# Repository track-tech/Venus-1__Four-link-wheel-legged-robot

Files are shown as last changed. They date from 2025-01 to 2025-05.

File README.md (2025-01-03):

# 启明-1 四连杆轮腿机器人 | Venus-1  Four-link wheel-legged robot

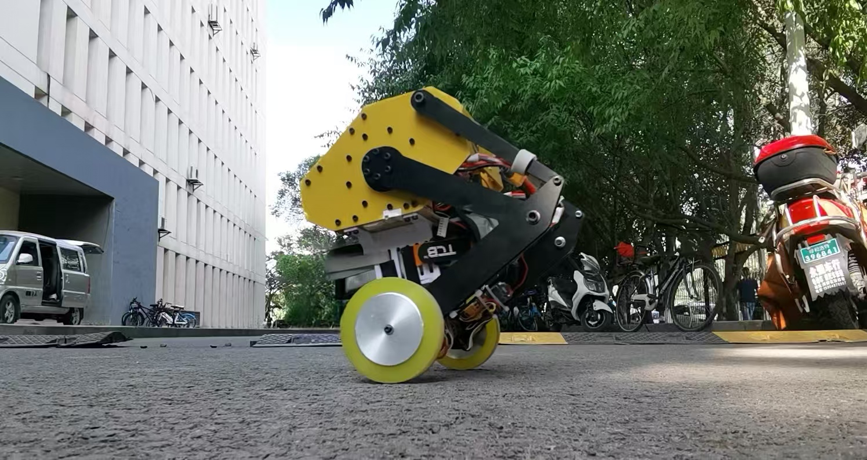
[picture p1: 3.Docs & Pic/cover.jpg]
Real Robot


## 0x00 声明&介绍

该项目为**个人本科毕业设计**，由于时间与个人能力不足，**存在设计缺陷**，请谨慎复刻。

项目遵循**GPL 3.0**协议，量产及商业使用需授权

> 演示视频合集
>[Venus轮腿机器人视频合集]: https://space.bilibili.com/21198864/lists/4193332?type=series
> 

**概况**

- 机械建模使用Soildworks2024 sp0.1绘制，使用请注意软件版本
- 基于STM32H723 HAL库开发，使用FreeRTOS进行任务管理
- 关节电机使用小米CyberGear微电机，轮电机使用DJI C610+M2006 P36
- 外壳及主要结构均使用3mm 3240环氧板（玻纤板），高强度
- 完全使用PID控制
- 机器人遥控使用FS-I6X 主控通过SBUS与接收机FS-IA6B通信
- 基本采用商业模块构件，拼装快速

------

### 机体测试

#### 重心自适应

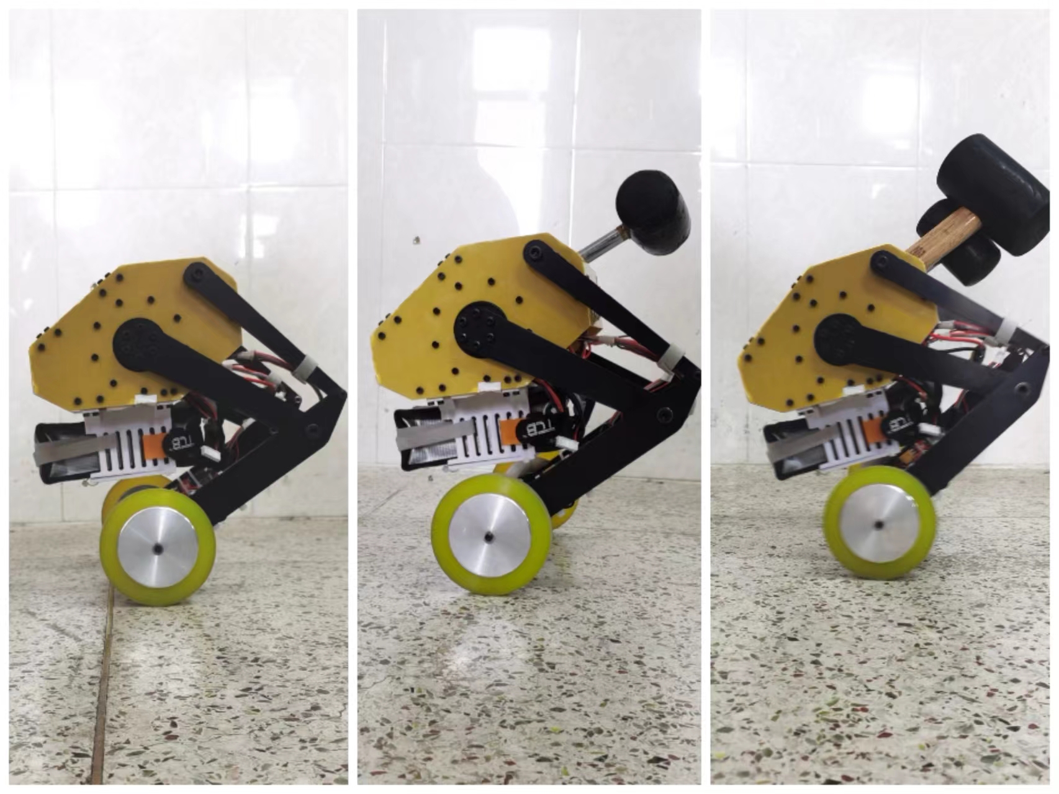
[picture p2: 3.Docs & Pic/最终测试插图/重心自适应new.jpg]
重心自适应new


#### 下落缓冲测试

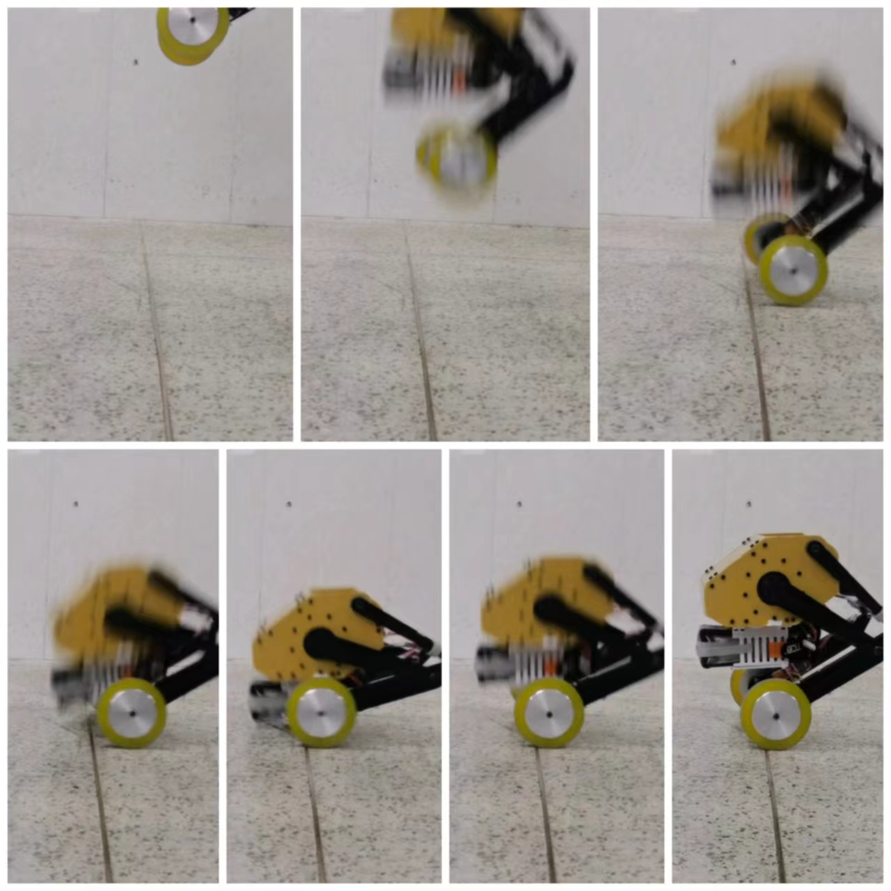
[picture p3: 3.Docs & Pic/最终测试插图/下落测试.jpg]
下落测试


#### 主动悬挂测试（Roll角自稳定）

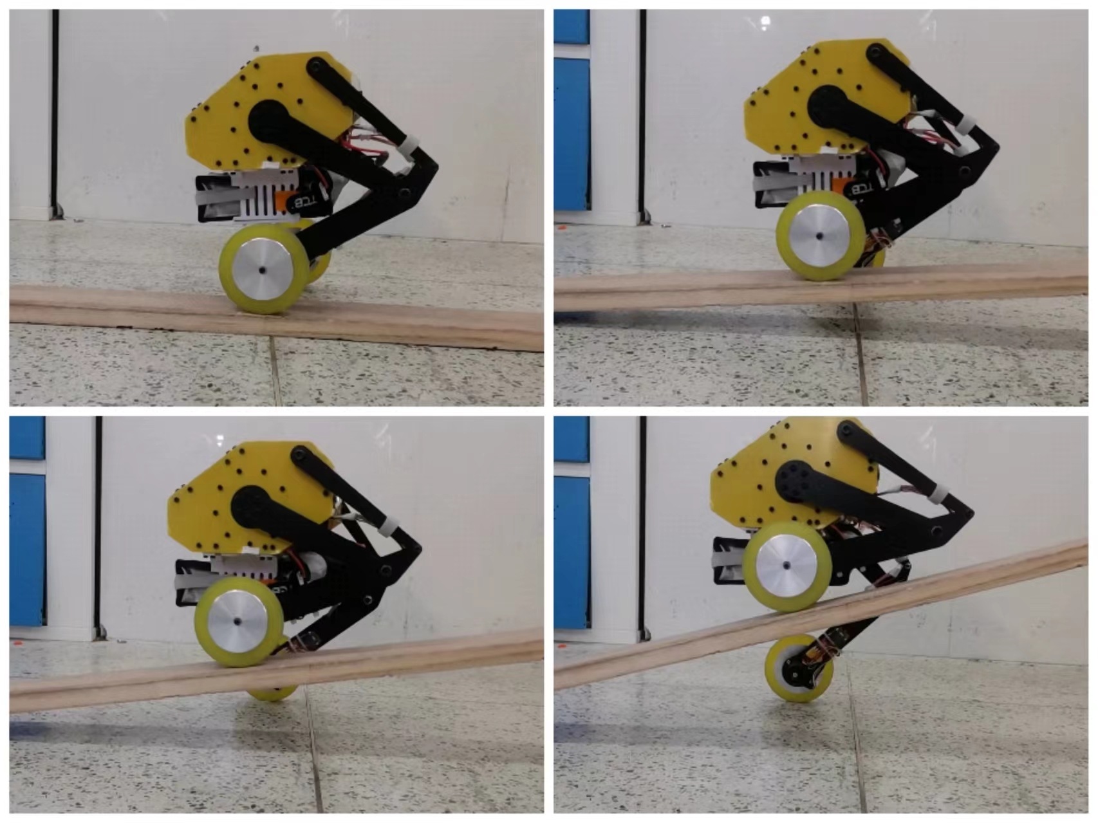
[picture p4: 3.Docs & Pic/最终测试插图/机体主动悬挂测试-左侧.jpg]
机体主动悬挂测试-左侧


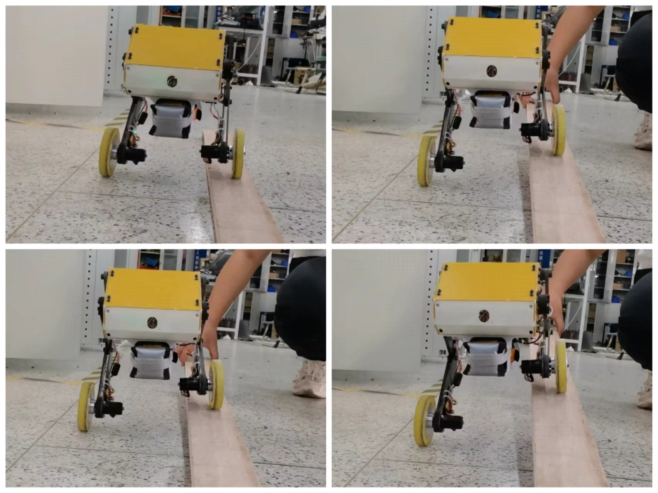
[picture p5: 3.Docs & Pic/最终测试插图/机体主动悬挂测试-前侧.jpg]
机体主动悬挂测试-前侧


#### 跳跃测试

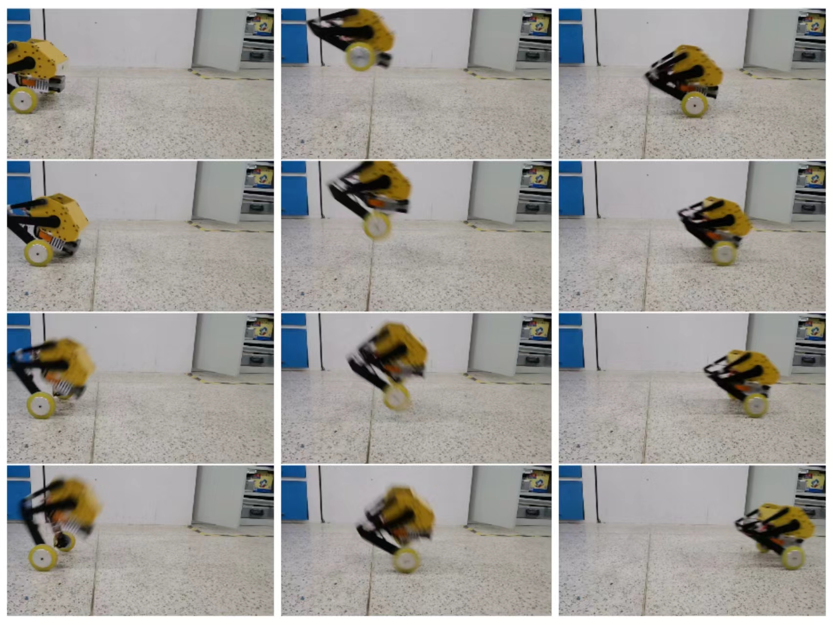
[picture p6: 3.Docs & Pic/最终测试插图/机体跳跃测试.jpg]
机体跳跃测试


## 0x01 机械结构

主体结构使用3mm 3240环氧树脂板及六面四方螺母固定，电气仓3D打印制成

### 连杆设计

连杆由Pyslvs拟合后，在Soildworks中建模

> [Pyslvs官网]: https://pyslvs-ui.readthedocs.io/en/stable/

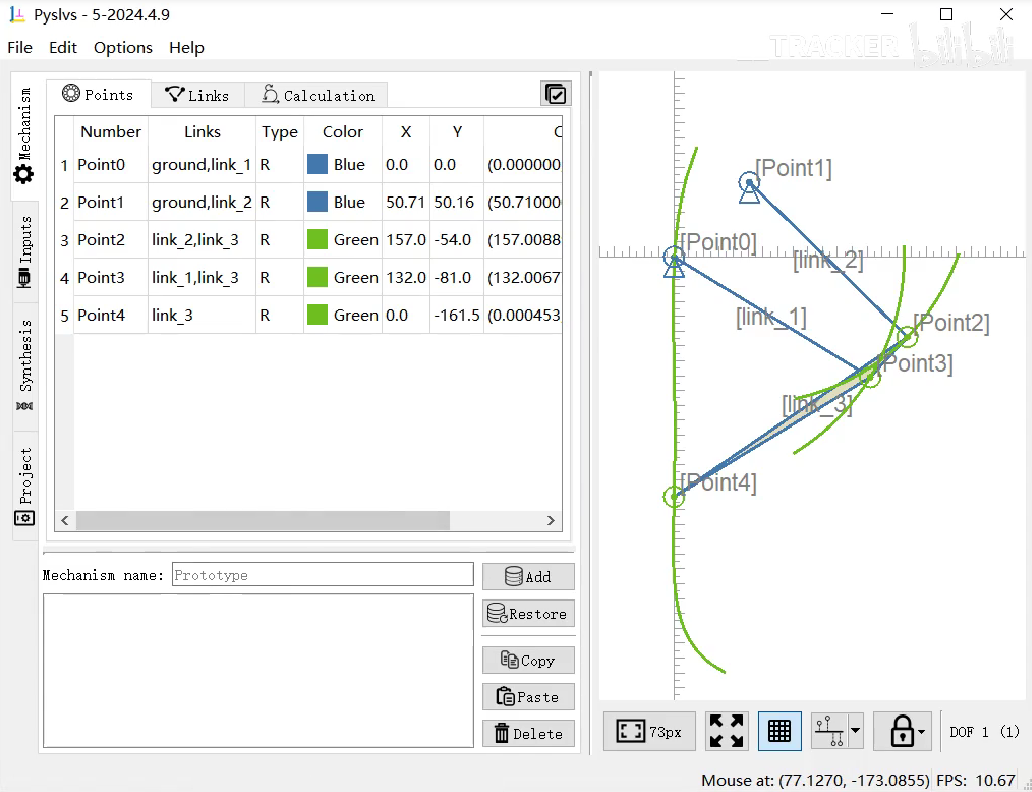
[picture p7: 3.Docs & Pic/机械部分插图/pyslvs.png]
pyslvs
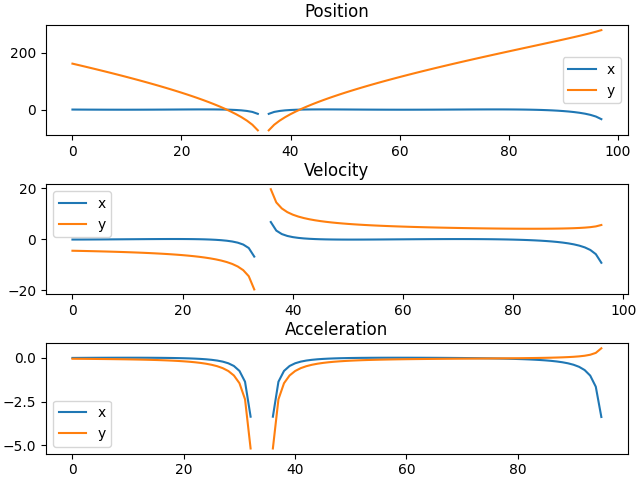
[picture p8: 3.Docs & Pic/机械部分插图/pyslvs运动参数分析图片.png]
pyslvs运动参数分析图片
|  |  |
| --- | --- |

### 三维简图

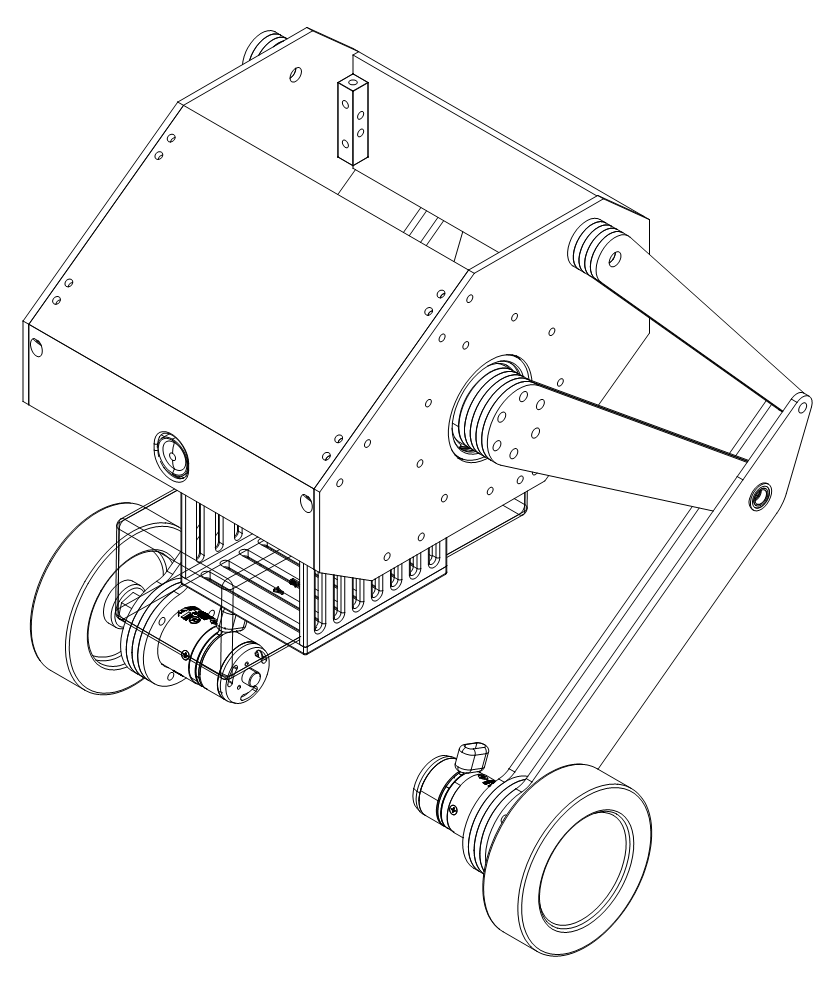
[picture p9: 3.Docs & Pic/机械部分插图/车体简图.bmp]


| 电器仓示意 | 截面视图 |
| :---: | :---: |
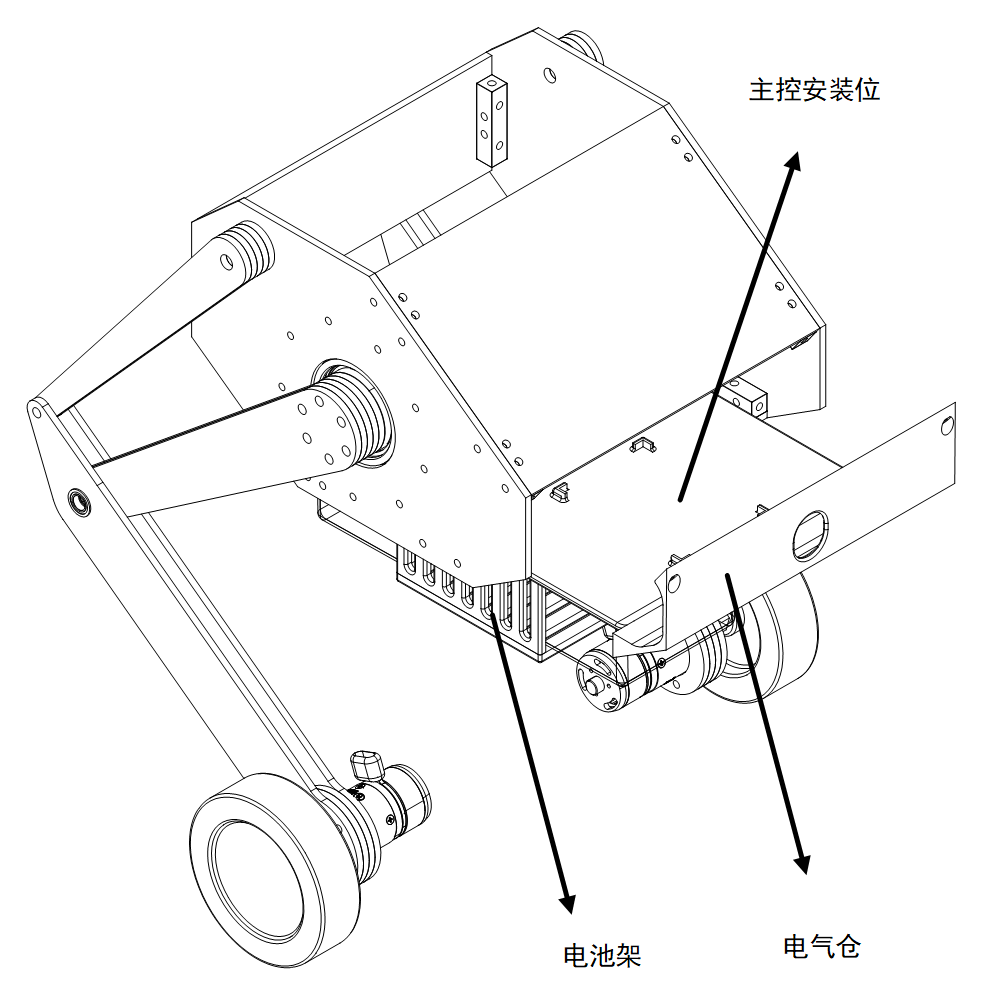
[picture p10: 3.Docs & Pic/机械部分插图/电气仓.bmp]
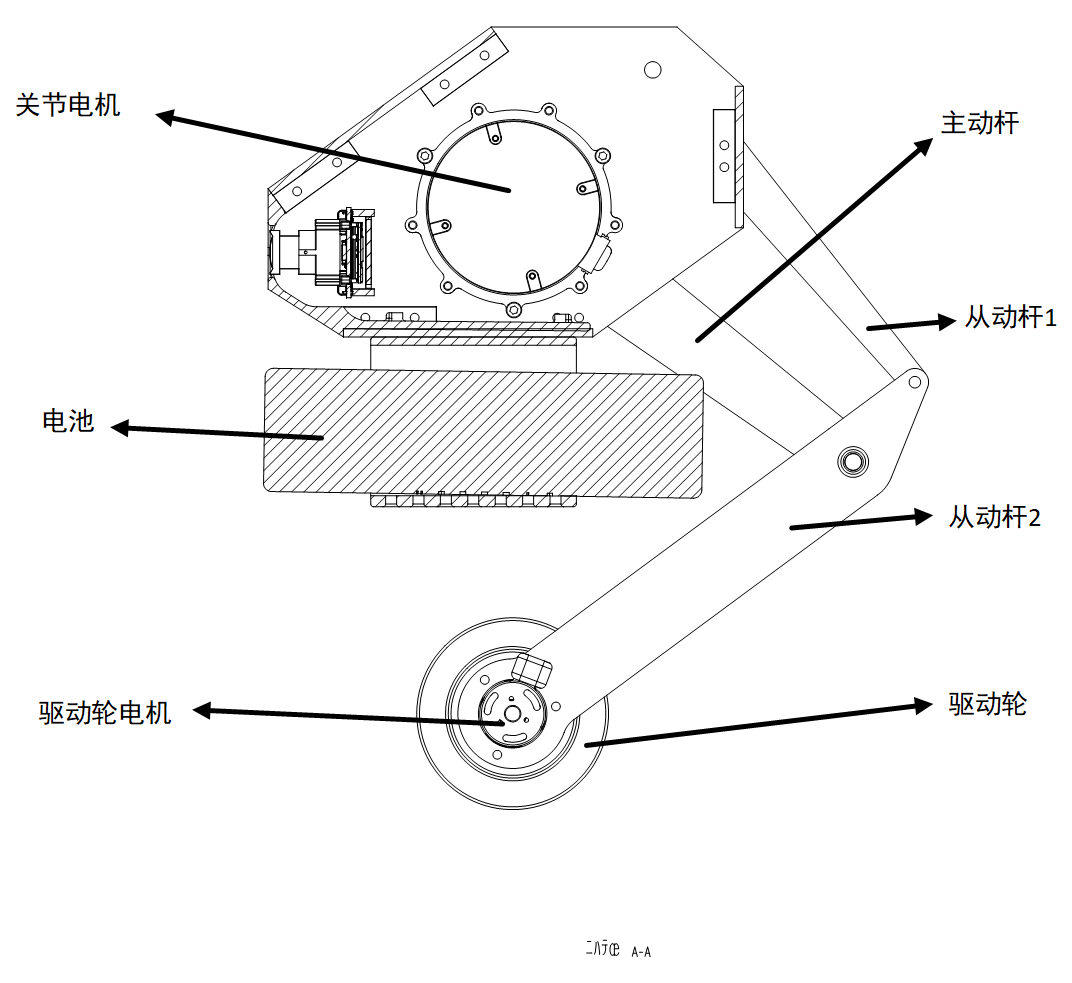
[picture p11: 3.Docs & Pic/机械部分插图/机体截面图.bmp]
|  |  |

## 0x02 电气连接

系统电源以及CAN总线通过中心分电板集合分配，下图为连接示意：

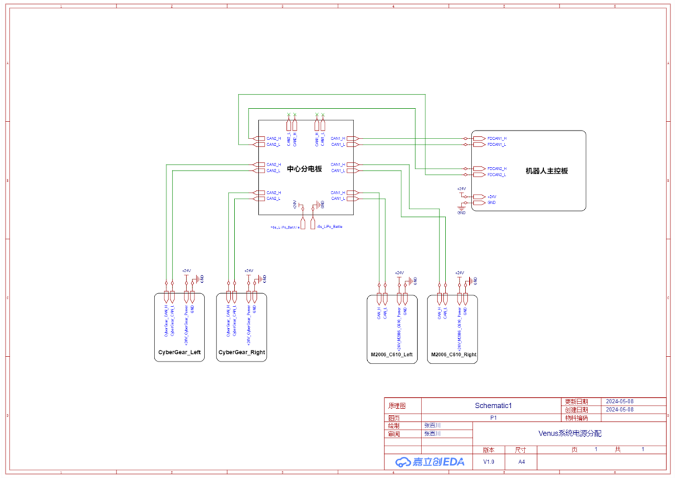
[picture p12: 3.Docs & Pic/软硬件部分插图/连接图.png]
连接图


使用到的中心分电板同样是之前顺便画的

>分电板开源链接
>[XT60/XT30分电板 | CAN Bus分线板]: https://oshwhub.com/marktracker/xt60-xt30-fen-dian-ban-can-fen-xian-ban
>
>

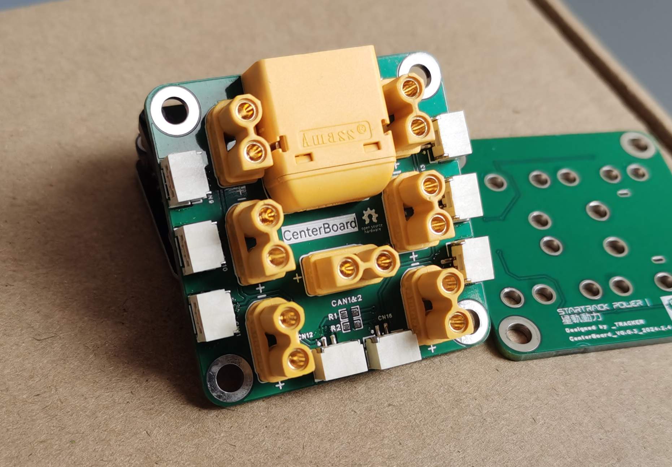
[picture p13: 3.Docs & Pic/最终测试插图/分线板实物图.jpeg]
分线板实物图


| 实物装配图-1 | 实物装配图-2 |
| :---: | :---: |
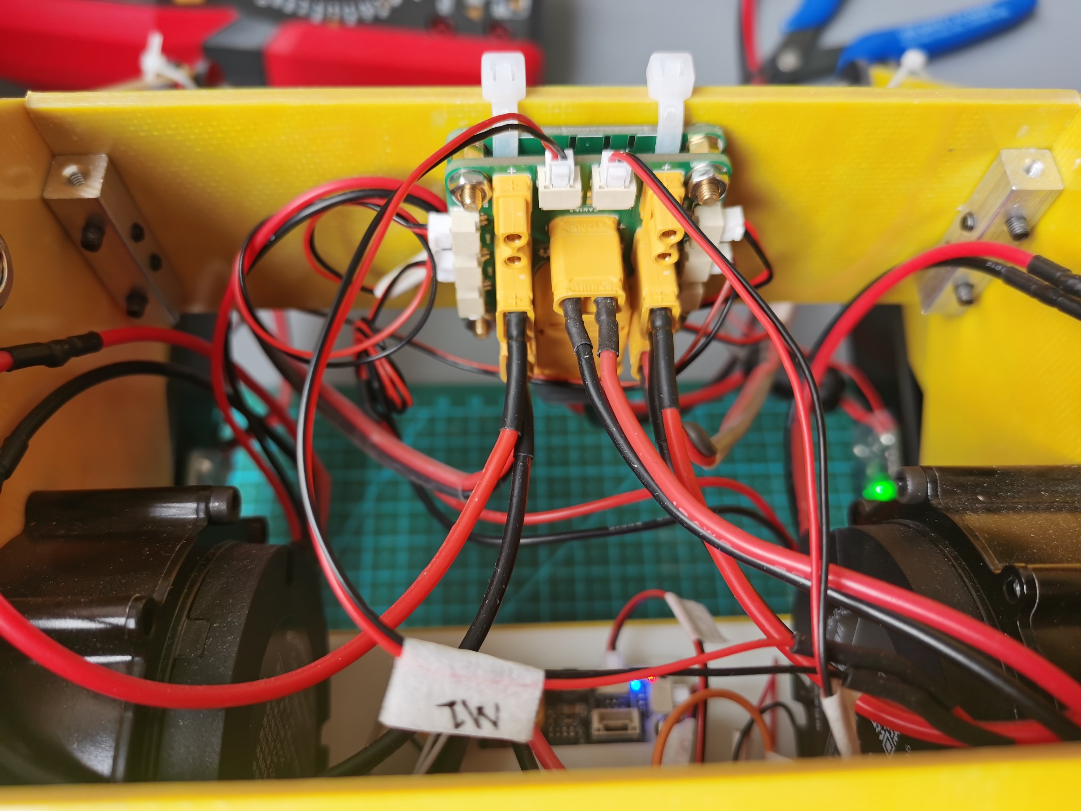
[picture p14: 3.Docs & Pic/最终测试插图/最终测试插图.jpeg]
最终测试插图
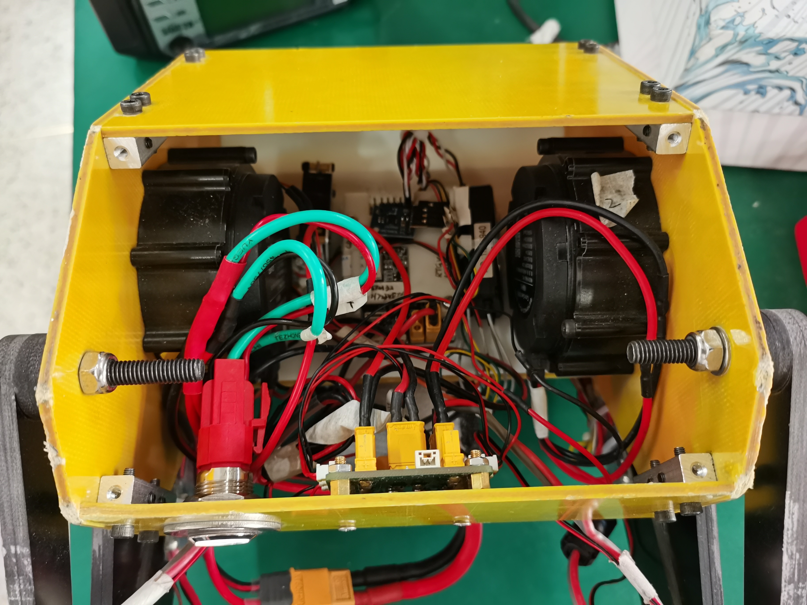
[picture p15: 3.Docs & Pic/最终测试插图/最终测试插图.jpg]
最终测试插图
|  |  |

## 0x03 软件架构

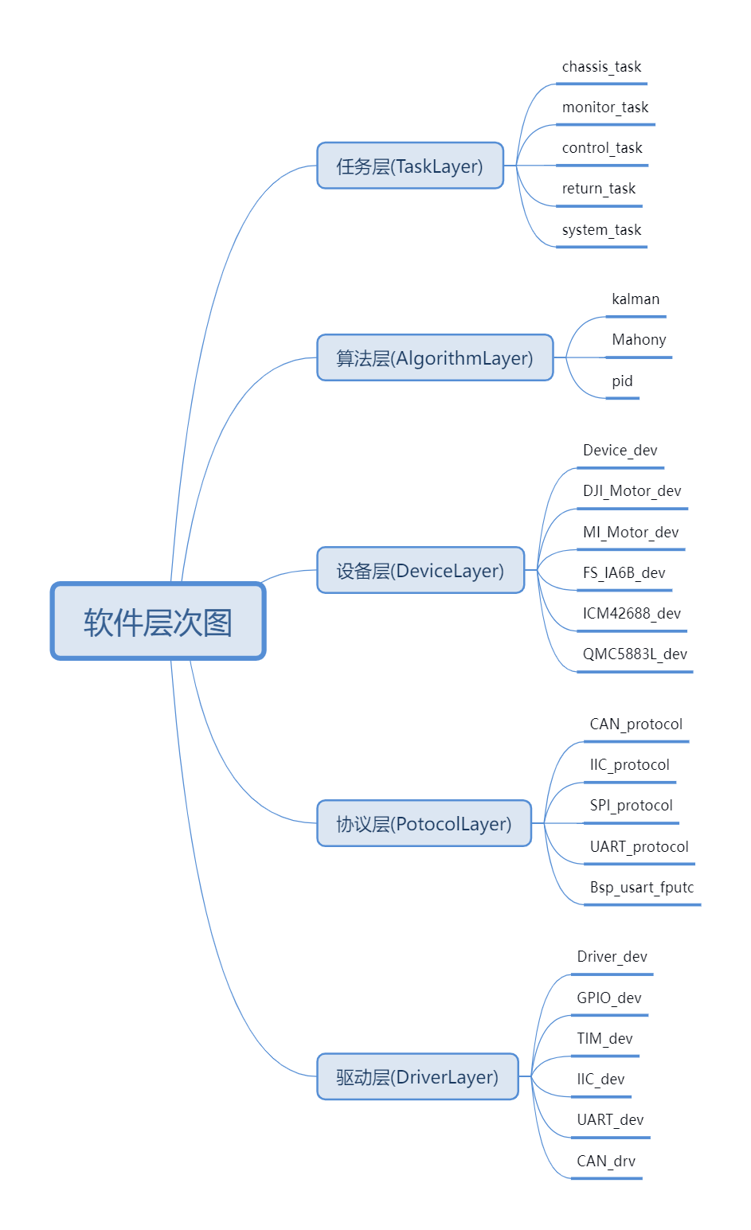
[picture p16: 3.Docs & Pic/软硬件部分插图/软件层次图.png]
软件层次图


软件整体分为五大块，具体见完整程序工程

## 0x04 参考成本&已知缺陷报告

### 参考成本表格

| 物料名 | 单价（RMB） | 数量 | 总价（RMB） |
| --- | --- | ---- | --- |
| CyberGear微电机 | 499 | 2 | 998 |
| DJI M2006动力套装（C610+M2006 P36） | 159+275=434 | 2 | 868 |
| 主控开发板 宇昌电子YCMC-H7A（STM32H723+ICM42688）/或改用达妙DM-MC02（STM32H723+BMI088 IMU型号不同，需重构） | 259(YCMC-H7A) | 1 | 259 |
| 3240环氧板定制费用（由于经过多次修改，具体费用不明，这里给出大致参考价格） | 200 | 1 | 200 |
| 轴承+螺栓螺母大致费用 | 40 | 1 | 40 |
| 中心分电板（自制嘉立创免费打板） | 10 | 1 | 10 |
| 连接用线束+接口 | 25 | 1 | 25 |
| 24V35C航模锂电 TCB | 176 | 1 | 176 |
| 遥控富斯FS-I6X+接收机FS-IA6B(遥控可替换为PS2无线遥控，或者其他类) | 251+56=301 | 1 | 301 |
| | | 合计 | 2877（除去遥控为2576） |

上述均为全新价格，可以去二手平台买旧的，可以更便宜

### 已知缺陷

**由于机器人现已放于学校，故无法进一步改进，下面是测试过程中发现的一些问题用于参考**

- 选用的驱动轮电机M2006减速箱齿隙较大，导致整体机身会在平衡点高速抖动，难以改善，我选用这个完全是由于经济条件限制，用了之前的旧电机，推荐直接使用大扭矩的云台电机作为驱动轮电机
- CyberGear为单编码电机，每次重新上电需要重新标定机械零点，该机器人通过轮电机与主体底板的限制，通过监测关节电机扭矩变化来确定是否到达零点，没有添加额外的限位块
- 演示视频与建模使用的轮并不一致，实物使用聚氨酯包胶轮规格 直径90mm 轮胶面宽16mm 内径6mm ，实测连接不稳定，最好使用3D打印轮毂，自制包胶轮
- Yaw轴漂移未解决，使用的CyberGear电机概率出现初始化指令不接收，原因未知，电机群群友似乎也有这种情况
- 电器仓正面开的洞是为M2Dock准备的，用于目标识别和路径跟踪（最后没时间加了）

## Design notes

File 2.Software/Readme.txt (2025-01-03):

工程文件使用STM32CubeMX生成基础框架&移植FreeRTOS，使用KEIL5编辑工程文件
任务函数运行周期见cubemx配置

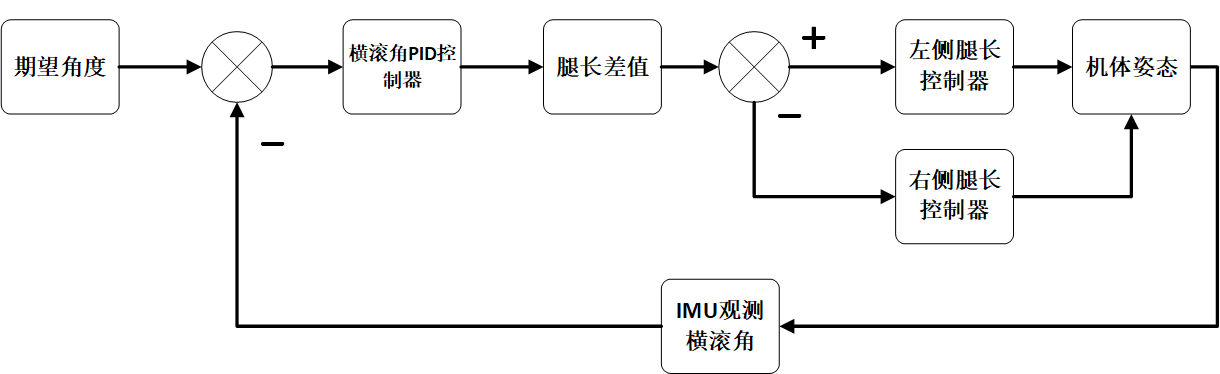
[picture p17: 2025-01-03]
3.Docs & Pic/控制部分插图/横滚角控制器.bmp

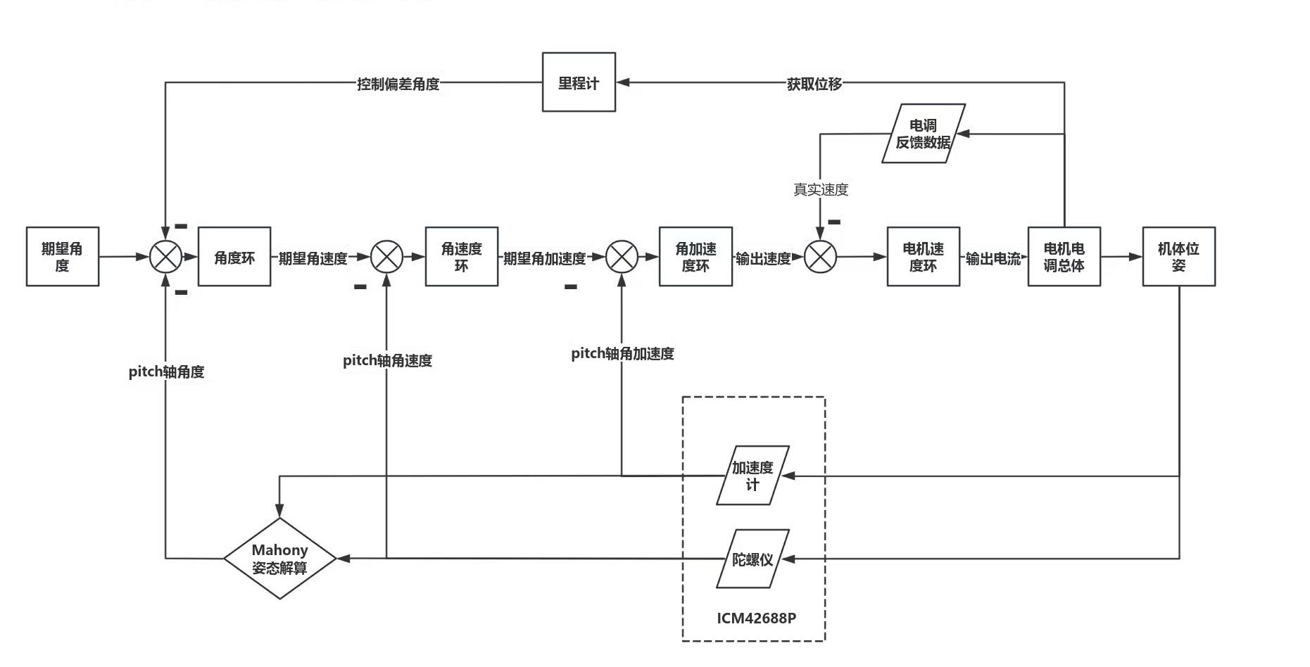
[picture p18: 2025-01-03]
3.Docs & Pic/控制部分插图/PID平衡控制器.jpg

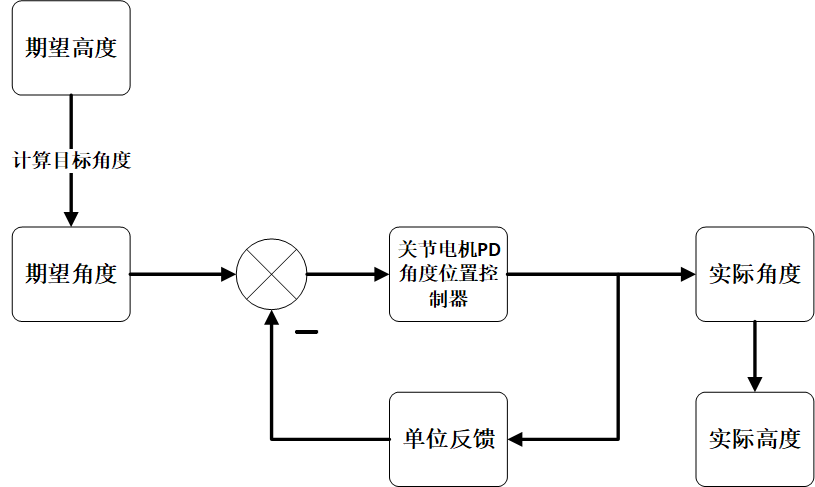
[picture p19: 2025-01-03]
3.Docs & Pic/控制部分插图/单腿高度控制.bmp

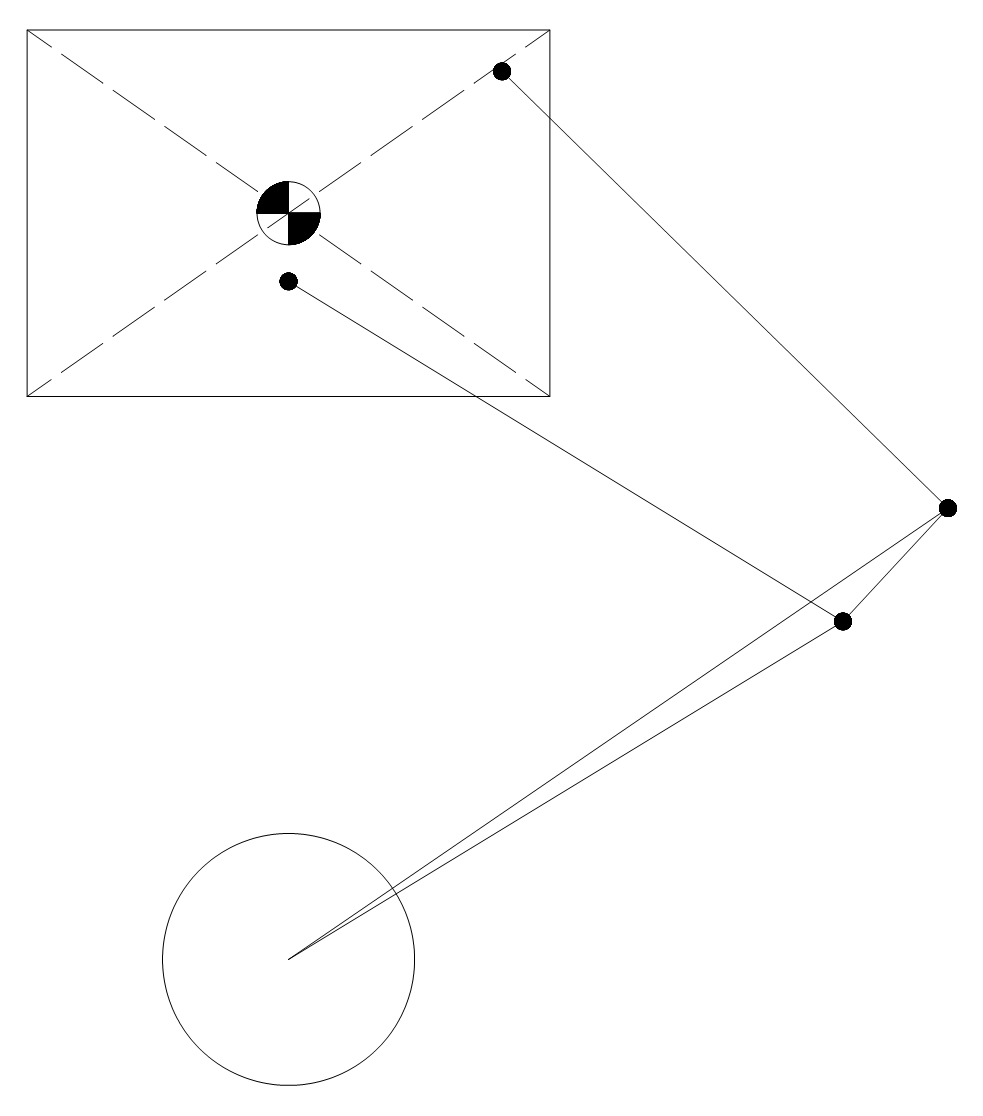
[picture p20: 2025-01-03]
3.Docs & Pic/机械部分插图/机器人简图.bmp

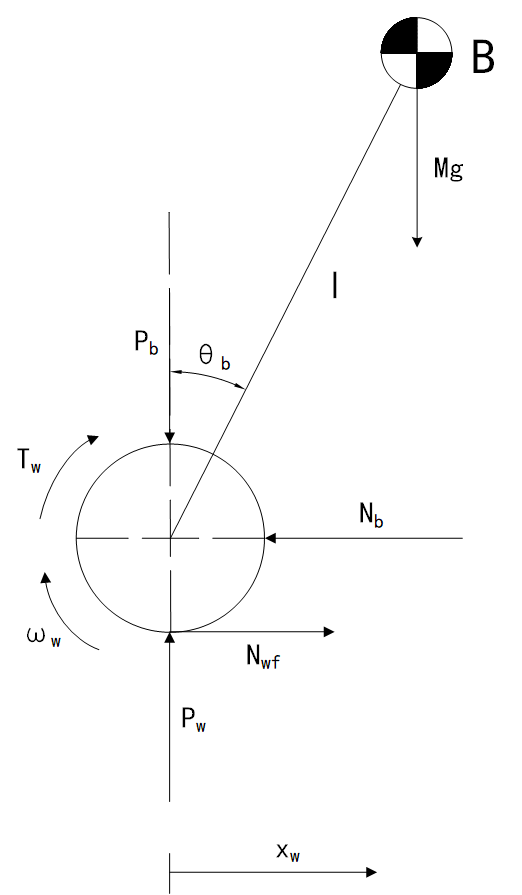
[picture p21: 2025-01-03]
3.Docs & Pic/机械部分插图/建模简图.bmp

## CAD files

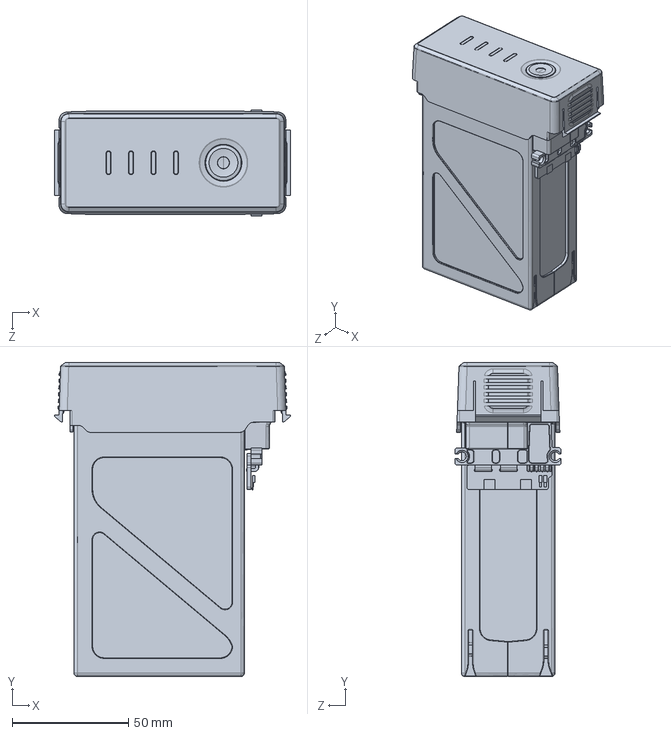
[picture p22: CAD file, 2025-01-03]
1.3D_Model/大疆电池-弃用/电池装配.SLDASM
101.5 x 134.8 x 45.5 mm

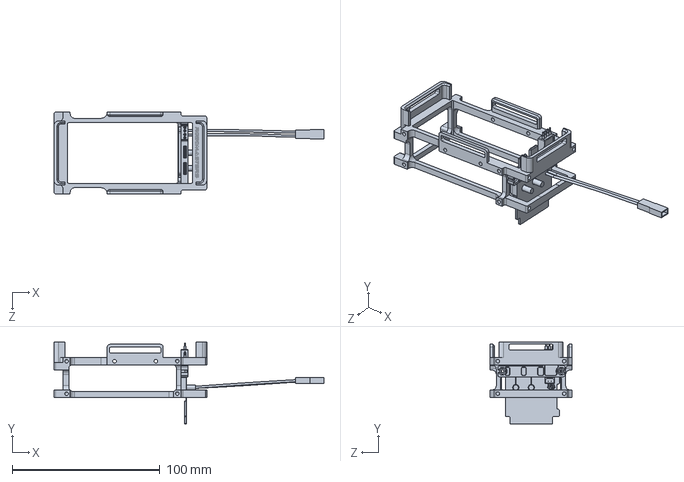
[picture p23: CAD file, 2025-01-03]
1.3D_Model/大疆电池-弃用/Rm新版电池架（带开关）.SLDPRT
182.9 x 55.5 x 55.4 mm

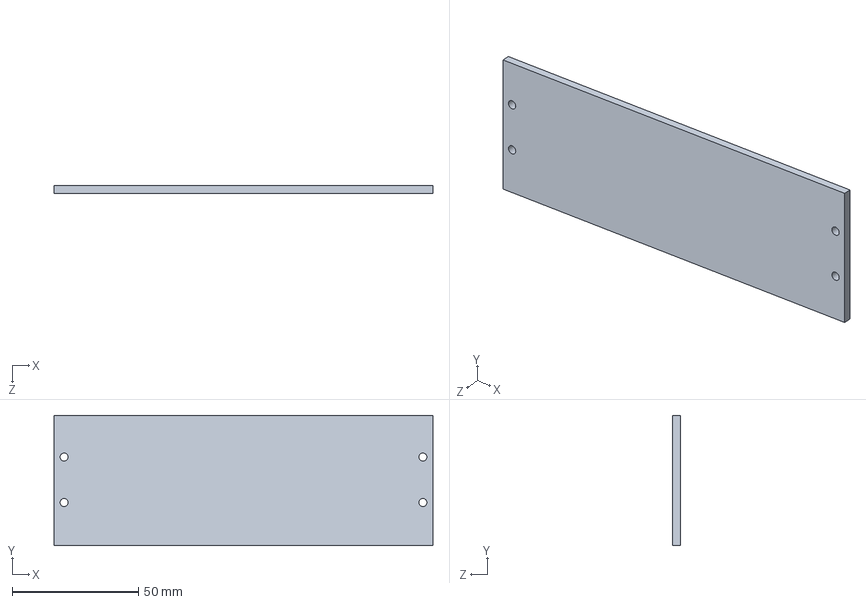
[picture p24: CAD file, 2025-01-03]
1.3D_Model/机架/后盖板^Venus_总装设计_原比例0.6倍_2023.10.17.SLDPRT
150.0 x 51.6 x 3.00 mm

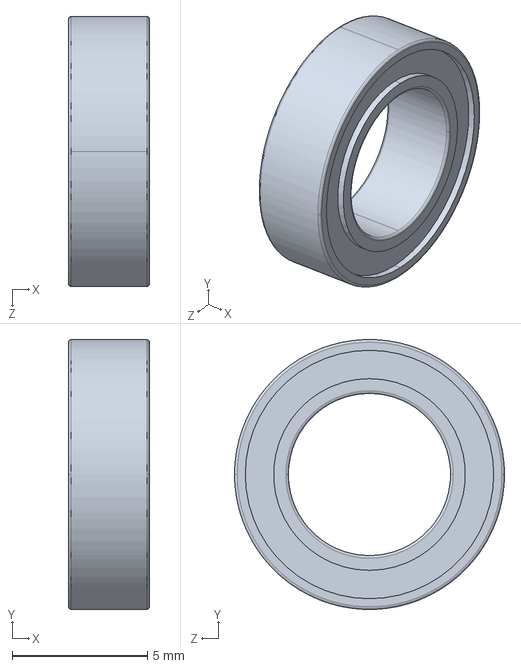
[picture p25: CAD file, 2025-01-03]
1.3D_Model/深沟球轴承 bca bcas[bca-a6-d10-b3].SLDPRT
3.00 x 10.0 x 10.0 mm

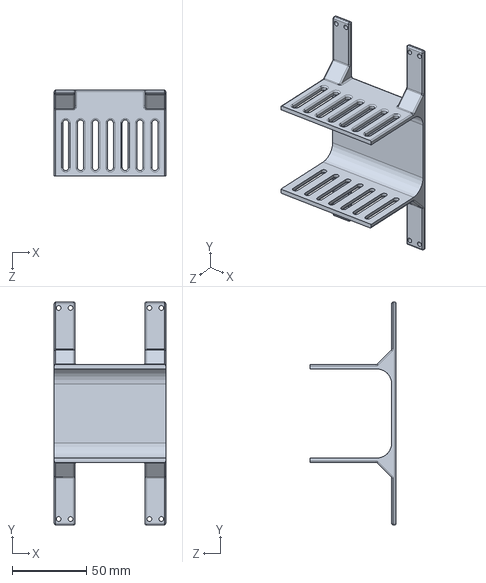
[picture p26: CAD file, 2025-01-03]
1.3D_Model/电池支架拆分/电池支架底座.SLDPRT
75.0 x 150.0 x 58.0 mm

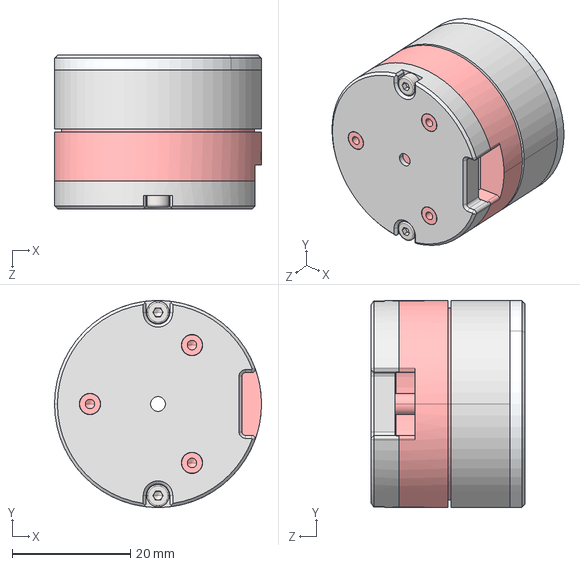
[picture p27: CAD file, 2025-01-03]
1.3D_Model/脉塔电机模型-原方案/2806/RMD-2806.STEP
35.0 x 35.0 x 26.0 mm

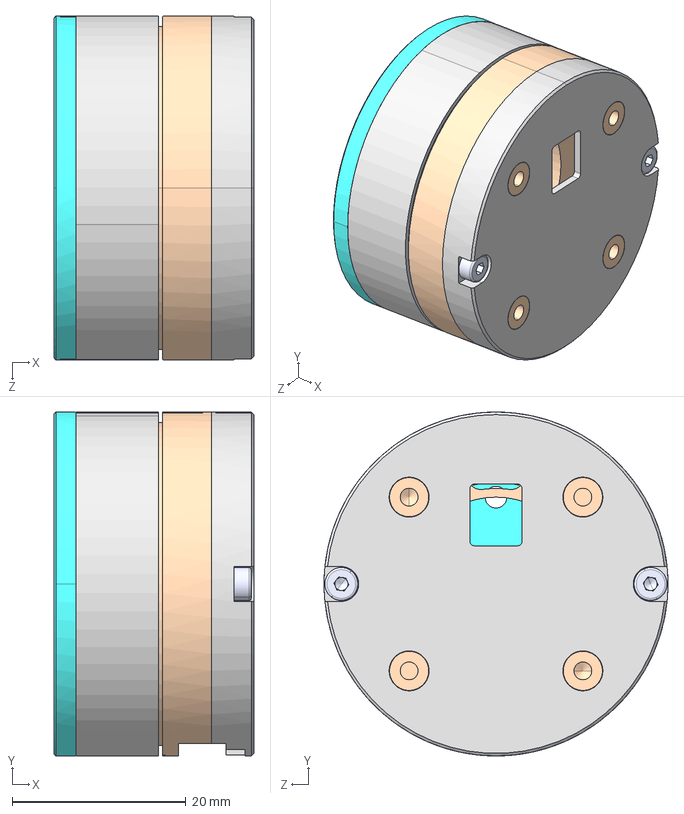
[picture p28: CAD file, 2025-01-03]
1.3D_Model/脉塔电机模型-原方案/4005/RMD-4005 .STEP
23.0 x 39.6 x 39.6 mm

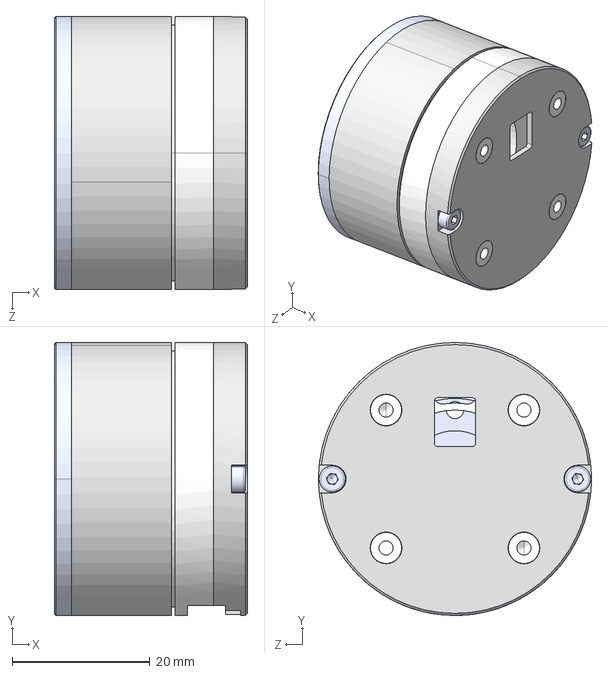
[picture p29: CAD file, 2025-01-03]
1.3D_Model/脉塔电机模型-原方案/4010/RMD-4010.STEP
28.0 x 39.6 x 39.6 mm

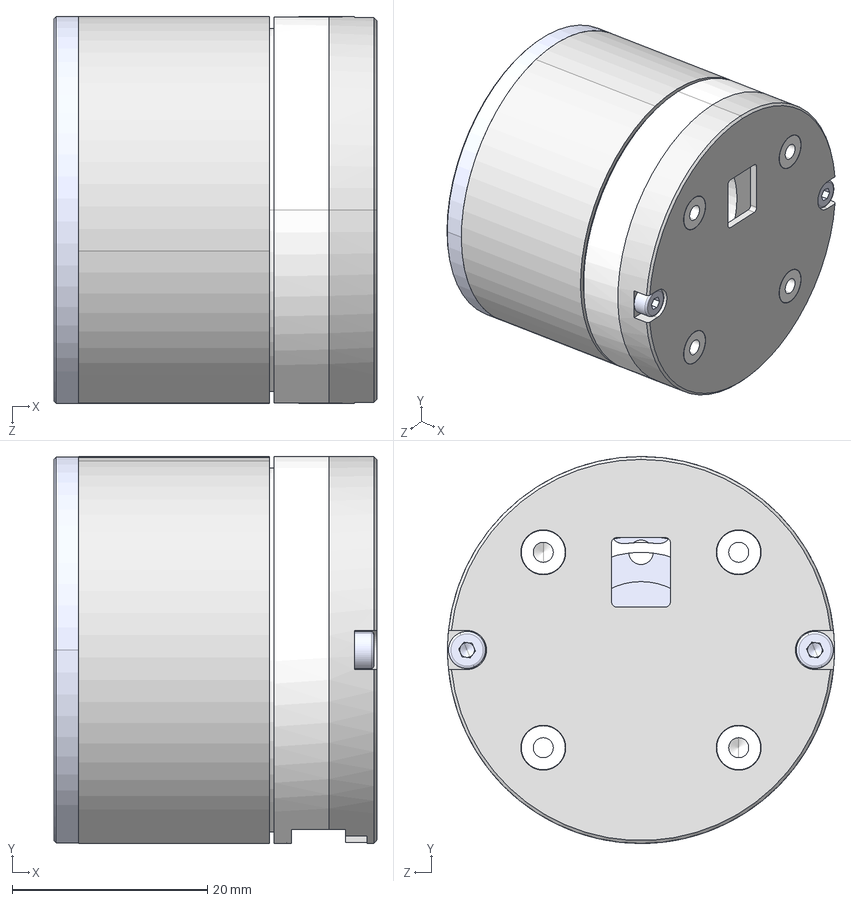
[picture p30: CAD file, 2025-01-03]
1.3D_Model/脉塔电机模型-原方案/4015/RMD-4015.STEP
33.0 x 39.6 x 39.6 mm

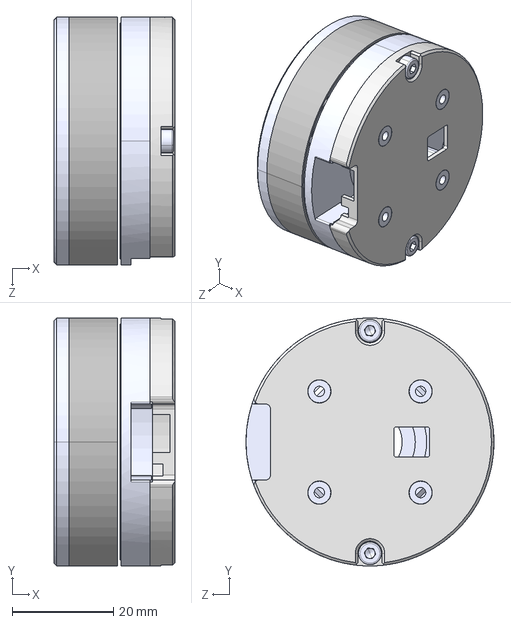
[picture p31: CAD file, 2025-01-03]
1.3D_Model/脉塔电机模型-原方案/5005/RMD-S-5005.STEP
23.9 x 49.0 x 49.0 mm

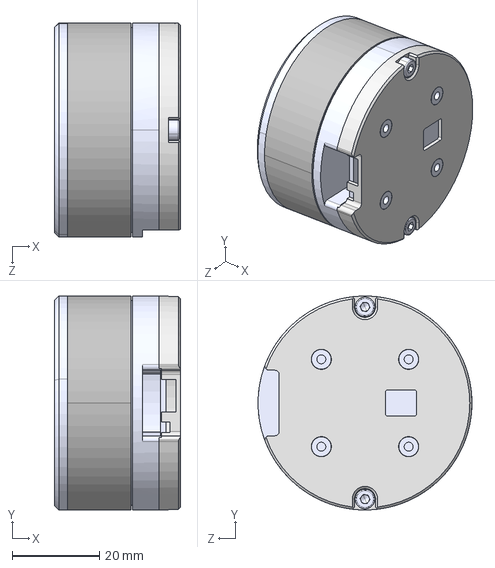
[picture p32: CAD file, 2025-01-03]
1.3D_Model/脉塔电机模型-原方案/5010/RMD-L-5010.STEP
28.9 x 49.0 x 49.0 mm

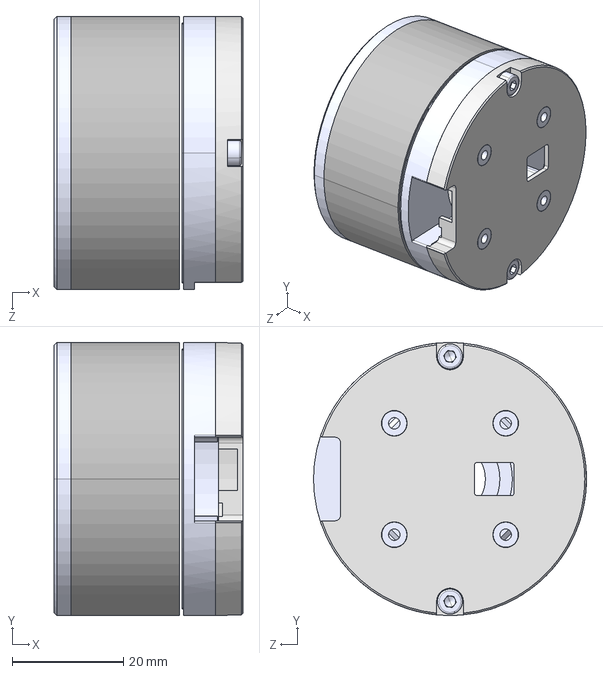
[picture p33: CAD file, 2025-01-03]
1.3D_Model/脉塔电机模型-原方案/5015/RMD-S-5015.STEP
33.9 x 49.0 x 49.0 mm

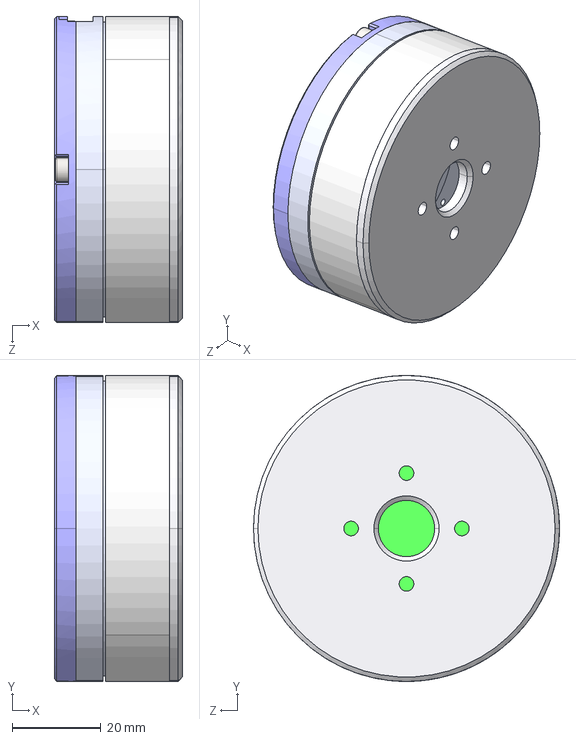
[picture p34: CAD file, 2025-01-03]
1.3D_Model/脉塔电机模型-原方案/7010/RMD-7010.STEP
28.9 x 69.0 x 69.0 mm

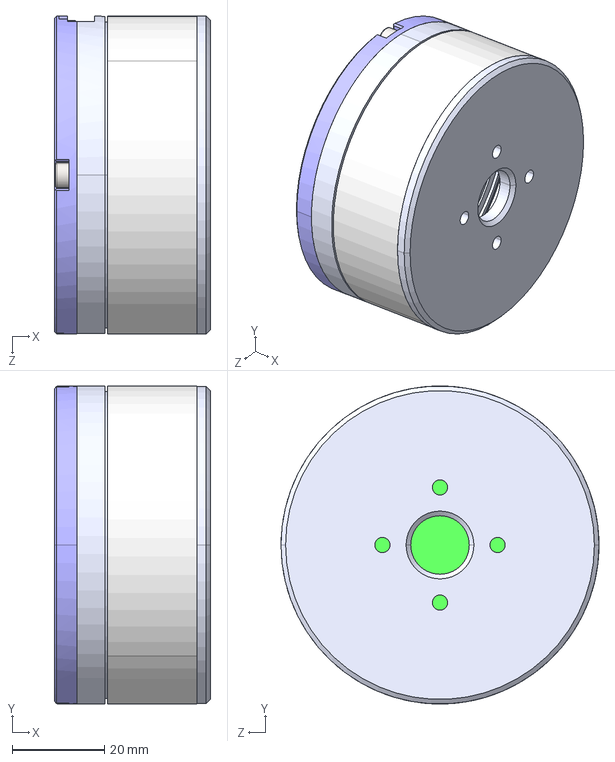
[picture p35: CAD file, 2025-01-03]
1.3D_Model/脉塔电机模型-原方案/7015/RMD-7015.STEP
33.9 x 69.0 x 69.0 mm

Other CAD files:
1.3D_Model/工程图-弃用/Venus_总装设计_原比例0.6倍_2023.10.17.DWG
1.3D_Model/脉塔电机模型-原方案/7025/RMD-7025.STEP
1.3D_Model/脉塔电机模型-原方案/9010/RMD-9010.STEP
1.3D_Model/脉塔电机模型-原方案/9015/RMD-9015.STEP
1.3D_Model/D70mm胶轮.SLDPRT
1.3D_Model/GB╱T 6170-2015[1型六角螺母M3].sldprt
1.3D_Model/GB╱T 6170-2015[1型六角螺母M5].sldprt
1.3D_Model/GB╱T 882-2008[销轴 B型4×16].sldprt
1.3D_Model/GB╱T 882-2008[销轴 B型6×18].sldprt
1.3D_Model/GB╱T 91-2000[开口销1.6×10].sldprt
1.3D_Model/GB╱T 91-2000[开口销1×6].sldprt
1.3D_Model/六面四方螺母.SLDPRT
1.3D_Model/六面四方螺母M3_8-H8_22.SLDPRT
1.3D_Model/内六角杯头螺栓 SCA SCAS[SCA-M3-L14].step
1.3D_Model/内六角杯头螺栓 SCA SCAS[SCA-M3-L16].step
1.3D_Model/内六角杯头螺栓 SCA SCAS[SCA-M3-L5].step
1.3D_Model/内六角杯头螺栓 SCA SCAS[SCA-M4-L25].step
1.3D_Model/内六角杯头螺栓 sca scas[sca-m3-l14].SLDPRT
1.3D_Model/塞打螺栓6_18_M5.SLDPRT
1.3D_Model/大疆电池-弃用/RmCS-cjq电池-TB47D-V2.SLDPRT
1.3D_Model/工程图-弃用/主动杆^Venus_总装设计_原比例0.6倍_2023.10.17.DWG
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

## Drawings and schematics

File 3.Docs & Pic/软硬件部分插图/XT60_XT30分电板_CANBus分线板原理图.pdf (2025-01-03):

24V输出 | 24V输入

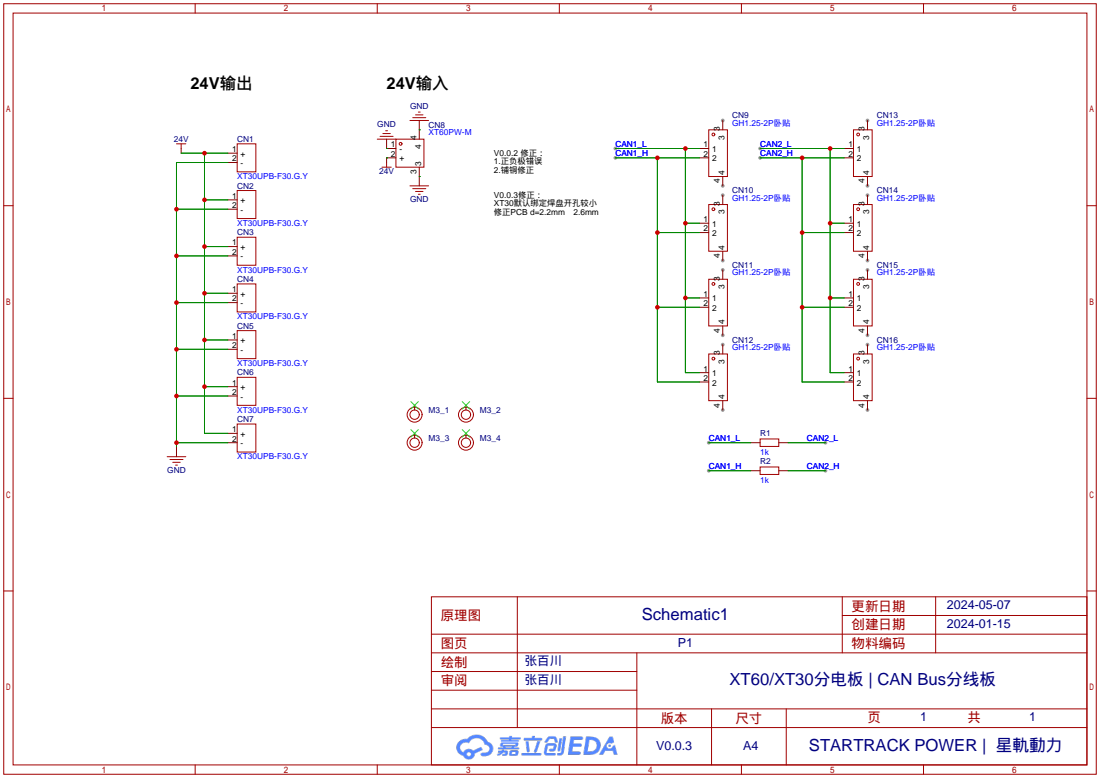
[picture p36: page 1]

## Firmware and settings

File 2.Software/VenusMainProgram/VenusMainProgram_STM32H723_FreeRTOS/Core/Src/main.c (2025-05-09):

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
/* Includes ------------------------------------------------------------------*/
#include "main.h"
#include "cmsis_os.h"
#include "fdcan.h"
#include "i2c.h"
#include "spi.h"
#include "tim.h"
#include "usart.h"
#include "gpio.h"

/* USER CODE BEGIN Includes */

#include "Driver_drv.h" //驱动层头文件
#include "Device_dev.h" //设备层头文件

#include "Bsp_usart_fputc.h"

/* USER CODE END Includes */


void SystemClock_Config(void);
void PeriphCommonClock_Config(void);
void MX_FREERTOS_Init(void);
/**
  * @brief  The application entry point.
  * @retval int
  */
int main(void)
{

  /* MCU Configuration--------------------------------------------------------*/

  /* Reset of all peripherals, Initializes the Flash interface and the Systick. */
  HAL_Init();

  /* Configure the system clock */
  SystemClock_Config();

/* Configure the peripherals common clocks */
  PeriphCommonClock_Config();

  /* Initialize all configured peripherals */
  MX_GPIO_Init();
  MX_FDCAN1_Init();
  MX_FDCAN2_Init();
  MX_SPI2_Init();
  MX_TIM16_Init();
  MX_UART4_Init();
  MX_USART1_UART_Init();
  MX_TIM4_Init();
  MX_TIM8_Init();
  MX_I2C1_Init();
  /* USER CODE BEGIN 2 */

  /* 总外设初始化程序段 */


    Driver_Init(); //驱动层初始化
    Device_Init(); //设备层初始化
	
	
//    printf("----------Venus系统初始化完毕----------\r\n");
    printf("----------Venus System Initialization complete----------\r\n");

	

//    printf("----------IMU校准中----------\r\n");
//    
    HAL_Delay(1000);


  /* USER CODE END 2 */

  /* Init scheduler */
  osKernelInitialize();

  /* Call init function for freertos objects (in cmsis_os2.c) */
  MX_FREERTOS_Init();

  /* Start scheduler */
  osKernelStart();

  /* We should never get here as control is now taken by the scheduler */

  /* Infinite loop */
  /* USER CODE BEGIN WHILE */
  while (1)
  {
    /* USER CODE END WHILE */

    /* USER CODE BEGIN 3 */


    
  }
  /* USER CODE END 3 */
}

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
/**
  * @brief  Period elapsed callback in non blocking mode
  * @note   This function is called  when TIM6 interrupt took place, inside
  * HAL_TIM_IRQHandler(). It makes a direct call to HAL_IncTick() to increment
  * a global variable "uwTick" used as application time base.
  * @param  htim : TIM handle
  * @retval None
  */
void HAL_TIM_PeriodElapsedCallback(TIM_HandleTypeDef *htim)
{
  if (htim->Instance == TIM6) {
    HAL_IncTick();
  }
}

/**
  * @brief  This function is executed in case of error occurrence.
  * @retval None
  */
void Error_Handler(void)
{
  /* USER CODE BEGIN Error_Handler_Debug */
  /* User can add his own implementation to report the HAL error return state */
  __disable_irq();
  while (1)
  {
  }
  /* USER CODE END Error_Handler_Debug */
}

#ifdef  USE_FULL_ASSERT
/**
  * @brief  Reports the name of the source file and the source line number
  *         where the assert_param error has occurred.
  * @param  file: pointer to the source file name
  * @param  line: assert_param error line source number
  * @retval None
  */
void assert_failed(uint8_t *file, uint32_t line)
{
  /* USER CODE BEGIN 6 */
  /* User can add his own implementation to report the file name and line number,
     ex: printf("Wrong parameters value: file %s on line %d\r\n", file, line) */
  /* USER CODE END 6 */
}
#endif /* USE_FULL_ASSERT */

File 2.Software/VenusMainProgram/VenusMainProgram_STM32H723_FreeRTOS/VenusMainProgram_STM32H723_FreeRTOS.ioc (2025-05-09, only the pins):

Mcu.UserName=STM32H723VETx
PA0.Signal=UART4_TX
PA13(JTMS/SWDIO).Signal=DEBUG_JTMS-SWDIO
PA14(JTCK/SWCLK).Signal=DEBUG_JTCK-SWCLK
PB12.Signal=FDCAN2_RX
PB13.Signal=FDCAN2_TX
PB14.Signal=USART1_TX
PB15.Signal=USART1_RX
PB6.Signal=I2C1_SCL
PB7.Signal=I2C1_SDA
PB8.Signal=S_TIM16_CH1
PB9.Signal=GPIO_Output
PC11.Signal=UART4_RX
PC14-OSC32_IN.Signal=RCC_OSC32_IN
PC15-OSC32_OUT.Signal=RCC_OSC32_OUT
PC2_C.Signal=SPI2_MISO
PC3_C.Signal=SPI2_MOSI
PC6.GPIO_Label=Buzzer_TlM8_CH1
PC6.Signal=S_TIM8_CH1
PC7.GPIO_Label=LED_R_TIM8_CH2
PC7.Signal=S_TIM8_CH2
PD0.Signal=FDCAN1_RX
PD1.Signal=FDCAN1_TX
PD14.GPIO_Label=LED_G_TlM4_CH3
PD14.Signal=S_TIM4_CH3
PD15.GPIO_Label=LED_B_TlM4_CH4
PD15.Signal=S_TIM4_CH4
PD3.Signal=SPI2_SCK
PD7.Signal=GPIO_Output
PE0.Signal=GPXTI0
PE1.Signal=GPXTI1
PE10.GPIO_Label=ENPower5V
PE10.Signal=GPIO_Output
PE14.GPIO_Label=USER_KEY
PE14.Signal=GPIO_Input
PH0-OSC_IN.Signal=RCC_OSC_IN
PH1-OSC_OUT.Signal=RCC_OSC_OUT

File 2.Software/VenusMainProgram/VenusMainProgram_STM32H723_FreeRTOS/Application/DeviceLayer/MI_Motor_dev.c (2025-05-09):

/**
 * @file MI_Motor_dev.c
 * @author __TRACKER (zhangbanzhuan@foxmail.com)
 * @brief 小米电机设备层驱动程序
 * @version 0.1
 * @date 2024-03-10
 * 
 * @copyright Copyright (c) 2024
 * 
 */
 
/* Includes -------------------------------------------------------------------*/

#include "MI_Motor_dev.h"
#include "CAN_drv.h"
#include "Bsp_usart_fputc.h"
#include <string.h>


/**
 * @brief 电机结构体初始化
 * 
 */
MI_Motor_s MI_Motor_1;
MI_Motor_s MI_Motor_2;



//F1 F4经典CAN使用
// CAN_TxHeaderTypeDef CAN_TxHeader_MI;
//H7 FDCAN使用
//FDCAN_TxHeaderTypeDef CAN_TxHeader_MI;

uint8_t MI_MASTERID = 1; //master id 发送指令时EXTID的bit8:15,反馈的bit0:7

/**
  * @brief          float转int，数据打包用
  * @param[in]      x float数值
  * @param[in]      x_min float数值的最小值
  * @param[in]      x_max float数值的最大值
  * @param[in]      bits  int的数据位数
  * @retval         none
  */
uint32_t FloatToUint(float x, float x_min, float x_max, int bits)
{
    float span = x_max - x_min;
    float offset = x_min;
    if(x > x_max) x=x_max;
    else if(x < x_min) x=x_min;
    return (uint32_t) ((x-offset)*((float)((1<<bits)-1))/span);
}

/**
  * @brief          输入范围限制
  * @param[in]      x 输入数值
  * @param[in]      x_min 输入数值的最小值
  * @param[in]      x_max 输入数值的最大值
  * @retval         none
  */
float RangeRestrict(float x, float x_min, float x_max)
{
    float res;
    if(x > x_max) res=x_max;
    else if(x < x_min) res=x_min;
    else res = x;
    return res;
}

/**
  * @brief          小米电机初始化 适用于F1 F4 经典CAN
  * @param[out]     hmotor 电机结构体
  * @param[in]      phcan can总线句柄
  * @retval         none
  */
// void MI_motor_Init(MI_Motor_s* hmotor,CAN_HandleTypeDef *phcan, uint8_t motor_id)
// {
//     hmotor->phcan = phcan;
//     hmotor->motor_id = motor_id;
// }

/**
  * @brief          小米电机初始化 适用于H7 FDCAN
  * @param[out]     hmotor 电机结构体
  * @param[in]      phcan can总线句柄
  * @retval         none
  */
void MI_motor_Init(MI_Motor_s* hmotor,FDCAN_HandleTypeDef *phcan, uint8_t motor_id)
{
    hmotor->phcan = phcan;
    hmotor->motor_id = motor_id;
}

/**
  * @brief          小米电机CAN通信发送 F1F4经典CAN
  * @param[in]      hmotor 电机结构体
  * @retval         none
  */
// void MI_motor_CanTx(MI_Motor_s* hmotor)
// {
//     CAN_TxHeader_MI.DLC = 8;
//     CAN_TxHeader_MI.IDE = CAN_ID_EXT;
//     CAN_TxHeader_MI.RTR = CAN_RTR_DATA;
//     CAN_TxHeader_MI.ExtId = *((uint32_t*)&(hmotor->EXT_ID));
//     /*检测可用的发送邮箱*/
//     uint32_t free_TxMailbox = HAL_CAN_GetTxMailboxesFreeLevel(hmotor->phcan);//检测是否有空闲邮箱
//     while (free_TxMailbox<3){//等待空闲邮箱数达到3
//         free_TxMailbox = HAL_CAN_GetTxMailboxesFreeLevel(hmotor->phcan);
//     }
//     /* 将发送信息添加到发送邮箱中 */
//     uint32_t mailbox;
//     HAL_CAN_AddTxMessage(hmotor->phcan, &CAN_TxHeader_MI, hmotor->txdata, &mailbox);//将发送的数据添加到发送邮箱中
// }

/**
  * @brief  小米电机CAN通信发送--适用于STM32H7(HAL库FDCAN兼容标准CAN)
  * @param  hmotor 电机结构体
  * @retval null
  */
void MI_motor_CanTx(MI_Motor_s* hmotor)
{
 
    CAN_TxHeader_MI.DataLength = FDCAN_DLC_BYTES_8;
    CAN_TxHeader_MI.IdType = FDCAN_EXTENDED_ID;             //扩展ID
    CAN_TxHeader_MI.TxFrameType = FDCAN_DATA_FRAME;         //数据帧
    CAN_TxHeader_MI.Identifier = *((uint32_t*)&(hmotor->EXT_ID));
	/*CAN_TxHeader_MI.ExtId = hmotor->EXT_ID.motor_id<<24 | hmotor->EXT_ID.data << 8 |          hmotor->EXT_ID.mode << 5;*/
    
    //新加
    CAN_TxHeader_MI.ErrorStateIndicator=FDCAN_ESI_ACTIVE;            
    CAN_TxHeader_MI.BitRateSwitch=FDCAN_BRS_OFF;               //关闭速率切换
    CAN_TxHeader_MI.FDFormat=FDCAN_CLASSIC_CAN;                //传统的CAN模式
    CAN_TxHeader_MI.TxEventFifoControl=FDCAN_NO_TX_EVENTS;     //无发送事件
    CAN_TxHeader_MI.MessageMarker=0; 
    
    
    /* Start the Transmission process */
    uint32_t ret = HAL_FDCAN_AddMessageToTxFifoQ(hmotor->phcan, &CAN_TxHeader_MI, hmotor->txdata);
    if (ret != HAL_OK) {
        /* Transmission request Error */
//        while(1);
        printf("FDCAN Transmission request Error");
    }
}


/*-------------------- 按照小米电机文档写的各种通信类型 --------------------*/

/**
  * @brief          获取设备ID （通信类型0），需在电机使能前使用
  * @param[in]      hmotor 电机结构体
  * @retval         none
  */
void MI_motor_GetID(MI_Motor_s* hmotor)
{
    hmotor->EXT_ID.mode = 0;
    hmotor->EXT_ID.data = 0;
    hmotor->EXT_ID.motor_id = 0;
    hmotor->EXT_ID.res = 0;
 
    for(uint8_t i=0; i<8; i++)
    {
        hmotor->txdata[i]=0;
    }
    
    MI_motor_CanTx(hmotor);
}

/**
  * @brief          运控模式电机控制指令（通信类型1）
  * @param[in]      hmotor 电机结构体
  * @param[in]      torque 目标力矩
  * @param[in]      MechPosition 
  * @param[in]      speed 
  * @param[in]      kp 
  * @param[in]      kd 
  * @retval         none
  */
void MI_motor_Control(MI_Motor_s* hmotor, float torque, float MechPosition , float speed , float kp , float kd)
{
    hmotor->EXT_ID.mode = 1;
    hmotor->EXT_ID.motor_id = hmotor->motor_id;
    hmotor->EXT_ID.data = FloatToUint(torque,T_MIN,T_MAX,16);
    hmotor->EXT_ID.res = 0;
 
    hmotor->txdata[0]=FloatToUint(MechPosition,P_MIN,P_MAX,16)>>8;
    hmotor->txdata[1]=FloatToUint(MechPosition,P_MIN,P_MAX,16);
    hmotor->txdata[2]=FloatToUint(speed,V_MIN,V_MAX,16)>>8;
    hmotor->txdata[3]=FloatToUint(speed,V_MIN,V_MAX,16);
    hmotor->txdata[4]=FloatToUint(kp,KP_MIN,KP_MAX,16)>>8;
    hmotor->txdata[5]=FloatToUint(kp,KP_MIN,KP_MAX,16);
    hmotor->txdata[6]=FloatToUint(kd,KD_MIN,KD_MAX,16)>>8;
    hmotor->txdata[7]=FloatToUint(kd,KD_MIN,KD_MAX,16);

    MI_motor_CanTx(hmotor);
}

/**
  * @brief          小米电机反馈帧解码（通信类型2）
  * @param[in]      Rx_can_info 接受到的电机数据结构体
  * @param[in]      rx_data[8] CAN线接收到的数据
  * @note           将接收到的CAN线数据解码到电机数据结构体中
  * @retval         none
  */
void MI_motor_RxDecode(RxCAN_info_type_2_s* RxCAN_info,uint8_t rx_data[8])
{
    uint16_t decode_temp_mi;//小米电机反馈数据解码缓冲
    decode_temp_mi = (rx_data[0] << 8 | rx_data[1]);
    RxCAN_info->angle = ((float)decode_temp_mi-32767.5)/32767.5*4*3.1415926f;;

    decode_temp_mi = (rx_data[2] << 8 | rx_data[3]);
    RxCAN_info->speed = ((float)decode_temp_mi-32767.5)/32767.5*30.0f;

    decode_temp_mi = (rx_data[4] << 8 | rx_data[5]);
    RxCAN_info->torque = ((float)decode_temp_mi-32767.5)/32767.5*12.0f;

    decode_temp_mi = (rx_data[6] << 8 | rx_data[7]);
    RxCAN_info->temperature = (float)decode_temp_mi/10.0f;
 }

/**
  * @brief          小米电机使能（通信类型 3）
  * @param[in]      hmotor 电机结构体
  * @retval         none
  */
void MI_motor_Enable(MI_Motor_s* hmotor)
{
    hmotor->EXT_ID.mode = 3;
    hmotor->EXT_ID.motor_id = hmotor->motor_id;
    hmotor->EXT_ID.data = MI_MASTERID;
    hmotor->EXT_ID.res = 0;
    for(uint8_t i=0; i<8; i++)
    {
        hmotor->txdata[i]=0;
    }

    MI_motor_CanTx(hmotor);
}
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

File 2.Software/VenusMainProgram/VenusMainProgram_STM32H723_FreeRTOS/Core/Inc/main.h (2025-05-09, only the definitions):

#define ENPower5V_Pin GPIO_PIN_10
#define ENPower5V_GPIO_Port GPIOE
#define USER_KEY_Pin GPIO_PIN_14
#define USER_KEY_GPIO_Port GPIOE
#define LED_G_TlM4_CH3_Pin GPIO_PIN_14
#define LED_G_TlM4_CH3_GPIO_Port GPIOD
#define LED_B_TlM4_CH4_Pin GPIO_PIN_15
#define LED_B_TlM4_CH4_GPIO_Port GPIOD
#define Buzzer_TlM8_CH1_Pin GPIO_PIN_6
#define Buzzer_TlM8_CH1_GPIO_Port GPIOC
#define LED_R_TIM8_CH2_Pin GPIO_PIN_7
#define LED_R_TIM8_CH2_GPIO_Port GPIOC

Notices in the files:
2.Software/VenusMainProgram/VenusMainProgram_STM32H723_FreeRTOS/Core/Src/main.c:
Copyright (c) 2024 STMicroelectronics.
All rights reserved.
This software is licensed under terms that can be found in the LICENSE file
